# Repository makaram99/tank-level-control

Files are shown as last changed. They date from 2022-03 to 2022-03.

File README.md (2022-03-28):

<h1 align="center">Tank Level Control</h1>

      

<p align="center">
Render
</p>

<sup>
  ✅ Perform a review and leave a comment <strong><a href="https://github.com/makaram99/tank-level-control/issues/5">here</a></strong><br>
  ✅ If you want to contribute, add a new record like <a href="contributing.md">here</a><br>
  ✅ If this needs to be improved, create an issue <strong><a href="https://github.com/makaram99/tank-level-control/issues">here</a></strong>
</sup>

---

<!-- @import "[TOC]" {cmd="toc" depthFrom=1 depthTo=6 orderedList=false} -->

<!-- code_chunk_output -->
## Table of Contents
- [Table of Contents](#table-of-contents)
- [🔑 Introduction](#introduction)
- [🧮 Block Diagram](#block-diagram)
- [➗ Calculations of Distance](#calculations-of-distance)
- [🛠️ Development Tools Required](#️-development-tools-required)
- [🗻 Project Hierarchy](#project-hierarchy)
- [⚙ Working](#working)
  - [Code](#code)
  - [Simulation](#simulation)
- [📑 Generate Documentation](#generate-documentation)
- [🏭 Manufacturing](#manufacturing)
- [🎯 Results](#results)
- [🔬 What is next?](#what-is-next)
- [💁‍♂️ Contribute](#️-contribute)
- [📞 Contact me](#contact-me)
- [📖 References](#references)
- [🔓 Licenses](#licenses)
- [🔏 Credits](#credits)

<!-- /code_chunk_output -->

---

## 🔑 Introduction

Tank Level Control System is a system designed to monitor and control the level of a fluid in a tank.

If the tank gets empty and filled periodically such as in **Residential Buildings** as shown in the image below.
It will be a boring task to get a human to monitor the tank. Also, human problems such as quick response is always slower than automation system. So, the automation system is the best solution for this problem.

<p align="center">
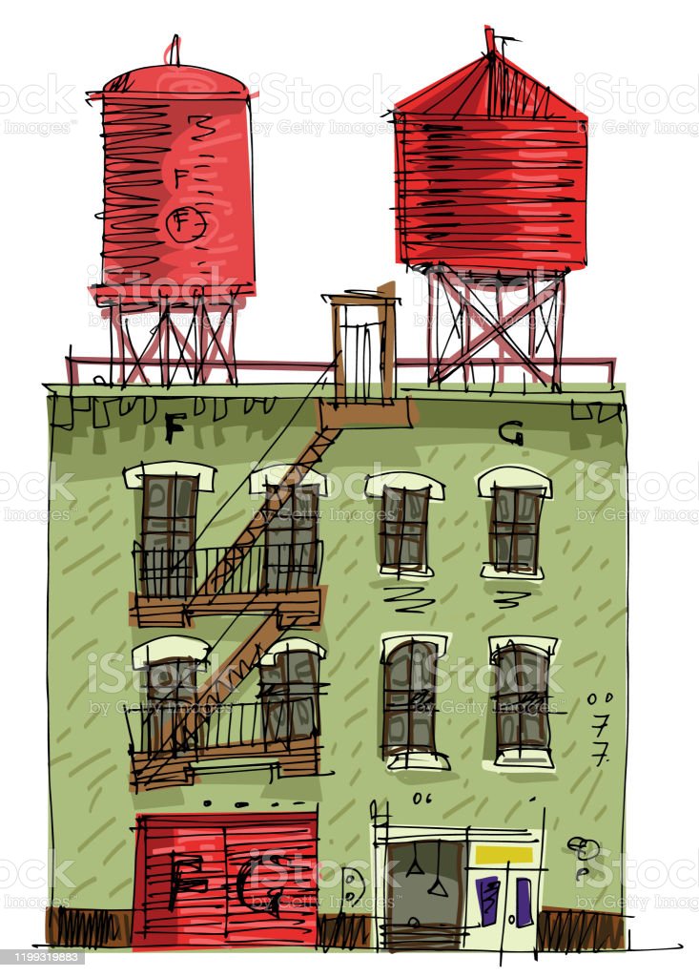
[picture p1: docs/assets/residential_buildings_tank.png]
residential_buildings_tank

</p>

It has many applications such:

1. Process tank: An important function.
2. Hot water tank: Water is removed, perhaps for washing down, and the level needs to be restored ready for the next wash cycle.

---

## 🧮 Block Diagram

<p align="center">
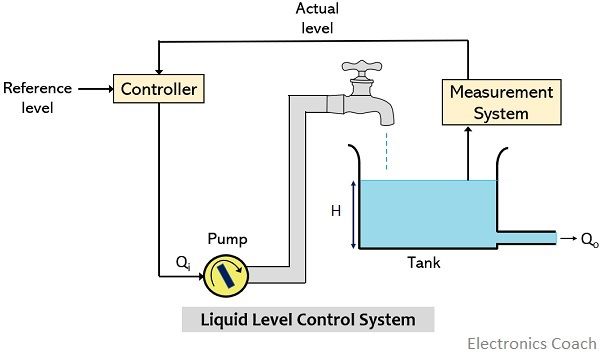
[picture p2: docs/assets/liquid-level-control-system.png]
System Construction
  
</p>

The main components of the system are:

1. **Fluid tank**: Used to hold the desired amount of fluid.
2. **Measurement system**: Senses the level of the fluid inside the tank.
3. **Controller**: Used to maintain the desired level by starting and stopping the pump depending on the information from the measurement system.
4. **Pump**: Feeds water from the source to the tank when actuated by the controller.

---

## ➗ Calculations of Distance

With the ultrasonic sensor, it sends ultrasonic waves which get beack to the sensor when hitting any surface (e.g., liquid in our case). The distance between the sensor and the surface is calculated by the following formula:

We can calculate the distance between the sensor and the surface as follows:

1. Calculate the time consumed from the instanse of sending the waves to the instance of recieving it using a timer inside the microcontroller.
2. As long as the ultrasonic waves are in fact sound waves. So, the speed of ultrasonic waves equals the speed of sound = **343 m/s**.
3. The distance between the sensor and the surface is:
   ```Distance = Speed * (Time / 2)```

4. Why the distance is divided by 2?
   The distance is divided by 2 because the waves go to the surface, then back to the sensor. So, the time calculated is the time it takes to go from the sensor to the surface and back to the sensor, hence the time must be divided by 2.

<p align="center">
  <img src="docs/assets/sensor_working.png" alt="Sensor Working"/>
</p>

---

## 🛠️ Development Tools Required

- **Toolchain**: MikroC Pro <img src="docs/assets/logo_mikro_c.png" alt="MickroC" height="40"/>

  MikroC Pro is used for code development and compiling the system.
  
  Website: [www.mikroe.com](http://www.mikroe.com/)

- **Text Editor**: <u>Visual Studio Code</u> <img src="docs/assets/logo_vscode.png" alt="VSCode" height="40"/>
  
  VS Code is used for code development. It is **free**.
  
  Download: [https://code.visualstudio.com/](https://code.visualstudio.com/)
  
- **Hardware Simulator**: <u>Proteus 8.9</u> <img src="docs/assets/logo_proteus.png" alt="Proteus" height="40"/>
  
  Proteus is used to simulate the hardware. So, no need to purchase any hardware.
  
  Download: [https://www.proteus.co.jp/](https://www.proteus.co.jp/)

- **Mechanical Design Software**: <u>SolidWorks</u> <img src="docs/assets/logo_solidworks.png" alt="SolidWorks" height="40"/>

  Website: [https://www.solidworks.com/](https://www.solidworks.com/)

- **PCB Design Software**: <u>Altium Designer</u> <img src="docs/assets/logo_altium.png" alt="Altium" height="40"/>

  Website: [https://www.altium.com/](https://www.altium.com/)

- **Documents Generator**: <u>doxygen</u> <img src="docs/assets/logo_doxygen.png" alt="doxygen" height="40"/>
  
  Doxygen is used to generate documentations of the code in html, latex, pdf, and other formats.
  
  Download: [https://www.doxygen.nl/download.html](https://www.doxygen.nl/download.html)

- **Command Line Automation Tool**: <u>make</u> <img src="docs/assets/logo_make.png" alt="make" height="40"/>
  
  Make is used to automate kernel commands.
  I've used it to automate the generation of documents from doxygen.
  
  Download:
  - Linux or MacOS: [https://www.gnu.org/software/make/](https://www.gnu.org/software/make/)
  - Windows: [http://gnuwin32.sourceforge.net/packages/make.htm](http://gnuwin32.sourceforge.net/packages/make.htm)

---

## 🗻 Project Hierarchy

The project contains some files and directories:

- **[electrical](electrical/)**: Contains everything about the electrical circuit.
  
  - [pcb](electrical/pcb): Contains PCB design of all electronics boards used in this project.
  - [simulation](electrical/simulation)**: Contains simulation files of all electronics boards used in this project.
  - [resources](electrical/resources): Contains all resources used while designing circuits.
  - [docs](electrical/docs): Contains videos of testing circuits, photos of circuits, and the pdf files describing the circuits.
  - [store_bills](electrical/store_bills): Contains store bills of components purchased for the project.
  - [bill_of_material.xlsx](electrical/bill_of_material.xlsx): Contains bill of material of components purchased for the project.
  - [version_edits.txt](electrical/version_edits.txt): Contains all bugs of the electronic circuits in the current version. So, they need to be fixed in the next version.

- **[mechanical](mechanical/)**: Contains everything about the mechanical design (Enclosure).
  - [box](mechanical/box): Contains the mechanical design of the enclosure using Solidworks.
  - [attachments](mechanical/attachments): Contains the external parts downloaded from the internet to incoroporate in the final assembly enclosure using Solidworks in the file [assembly.SLDASM](mechanical/assembly.SLDASM).
  - [arrows_keypad](mechanical/arrows_keypad), [control_circuit](mechanical/control_circuit), and [power_circuit](mechanical/power_circuit): Step files of the electronics circuits [here](electrical/simulation), to incoroporate in the final assembly enclosure using Solidworks in the file [assembly.SLDASM](mechanical/assembly.SLDASM).
  - [assembly.SLDASM](mechanical/assembly.SLDASM): Contains the final assembly of the projects containing enclosure, electronic circuits, and attachments.
  - [assembly_drawing.SLDDRW](mechanical/assembly_drawing.SLDDRW): Contains the drawing file generated by Solidworks for the assembly.
  - [final_assembly.PDF](mechanical/docs/final_assembly.PDF): Contains dimension, and different views of the assembly. It is generated from the file [final_assembly.PDF](mechanical/docs/final_assembly.PDF).

- **[software](software/)**: Contains everything about the code.
  - [code](software/code): Contains the code of the project.
  - [resources](electrical/resources): Contains all resources used while designing circuits.
  - [problems.txt](software/problems.txt): Contains documentation of some problems occuredd while testing the system physically.
  - [version_edits.txt](software/version_edits.txt): Contains all bugs of the code in the current version. So, they need to be fixed in the next version.

- **[docs](docs/)**: Contains the documentation generated using doxygen and make, and other documents designed by me.
- **[README.md](README.md)**: Contains the introduction of the project (What you are reading now).
- **[LICENSE](LICENSE)**: Contains the license of the project.
- **[Doxyfile](Doxyfile)**: Contains the configuration of doxygen (Documentation generator).
- **[doxygen.mk](doxygen.mk)**: Contains the configuration and rules to be run using make to generate documents.
- **[Makefile](Makefile)**: Contains the configuration and rules to be run using make to automate buil process of the software (compile, flash, clean, ...) documents.
- **[steps_of_project.pdf](steps_of_project.pdf)**: Contains the block diagram of steps of the project.

---

## ⚙ Working

### Code

To develop the project (code), you need to:

- YOU MUST HAVE **(MikroC Pro) or (Visual Studio Code with XC8 PIC Compiler)** installed on your computer.
- Open the [code](software/code) directory.
- If you have:
  - MikroC Pro: Click twice on **[tankLevel.mcppi](tankLevel.mcppi)** file. It will open with Mikro C Pro.
  - Visual Studio Code with XC8 compiler: Open the project with VS Code.
- Enjoy the development.
- To build the project, if you have:
  - MikroC Pro: Click on **Build button** on quick access bar of MikroC Pro, or press **Ctrl + F9** on the keyboard.
  - Visual Studio Code with XC8 compiler:
    - Open the terminal inside VS Code by pressing on **Ctrl + `** on the keyboard.
    - Type the command ```make all```. It will compile the project.
    - The hex file will be generated in the [code](software/code) directory with the name **app.hex**.
    - To flash the hex file to the PIC, type the command ```make flash```.
    - To remove the output files (hex and intermediate files), type the command ```make clean```.

**NOTE**: I've documented the code as much as I can. So, I hope you will understand the code.

### Simulation

To simulate the project, you need to:

- YOU MUST HAVE **Proteus** installed on your computer.
- Proteus has **compatibility issues** with its version, and the project may not be opened if you have a different version of proteus. So, you need to install **Proteus 8.9** to be able to simulate the project.
- From the [simulation](electrical/simulation) directory, open the folder of any of the boards.
- Click twice on the file ends with **[.pdsprj](simulation/simulation.pdsprj)**.
- It will open with Proteus as shown here:
  - Control Circuit
   <img src="electrical/docs/test_simulation/simulation_control_circuit.gif" alt="simulation_control_circuit"/>
  - Power Circuit
   <img src="electrical/docs/test_simulation/simulation_power_circuit.gif" alt="simulation_power_circuit"/>

- As shown in the Control Circuit, it is divided into blocks such as Controller, PUMP, and Sensor blocks.

- To run simulation, click on **F12** from the keyboard.
- Increase/Decrease the distance measured by the ultrasoni sensor by pressing Up/Down arrow on the Sensor block. The distance measured by the sensor will be displayed on the LCD screen as a percentage representing the level percentage of the tank. The percentage depends on a predetermined value equals to the height of the tank (in our case, the tank is 24cm height).
- When the percentage is lower than 15%, the pump will be turned on.
- When the percentage is higher than 80%, the pump will be turned off.
- When the percentage is between 15% and 80%, the pump will be latched to the last state. If the pump was on, it will be remains on. If the pump is off, it will remains off.
- To stop the simulation: Press twice on **ESC** key from the keyboard.

**NOTE**: The keypad is not used in the current version of the project. It is put for future use.

---

## 📑 Generate Documentation

To generate documentation:

1. YOU MUST HAVE **DOXYGEN** AND **MAKE** INSTALLED ON YOUR COMPUTER.
2. From the home directory of the project (**tank_level_control**), open the command prompt in your OS (**cmd** for Windows, **bash** for linux, ...)
3. Run the following command:
   ```make -f doxygen.mk all```
4. The documentation will be generated in the **[docs](docs)** directory.

---

## 🏭 Manufacturing

**Here is a comparison between CAD design on Solidworks versus the final physical shape:
**

1. Product:

  <img src="mechanical/docs/box_cad_vs_real_view2.png" alt="Enclosure" width="500"/>
2. Control Circuit:

  <img src="mechanical/docs/control_circuit_cad_vs_reality.png" alt="Control" width="500"/>
3. Power Circuit:

  <img src="mechanical/docs/power_circuit_cad_vs_real.png" alt="Power" width="500"/>
4. Keypad:

  <img src="mechanical/docs/keypdad_cad_vs_reality.png" alt="Keypad" width="500"/>

---

## 🎯 Results

After running the project either on the simulation (Proteus) or running the physical hardware. The result was as expected. So, you also can use the project and it will work as expected.

You can check the working of the project by opening the [test_project.m4v](electrical/docs/test_videos/test_project.m4v) file.

If you want to check operation of each circuit, open:

- [test_power_circuit.m4v](electrical/docs/test_videos/test_power_circuit.m4v) to see the working of power circuit.
- [test_kit.m4v](electrical/docs/test_videos/test_kit.m4v) to see the working of control circuit.
- [test_short_circuit.m4v](electrical/docs/test_videos/test_short_circuit.m4v) to see the working of short circuit protection.

---

## 🔬 What is next?

I will always try to improve this project.
***Next Version***: Features of the next version can be found in the file [version_edits.txt](software/version_edits.txt) in [software](software/) directory.

---

## 💁‍♂️ Contribute

If you want to contribute to the project, add a new record like <a href="contributing.md">here</a><br>

## 📞 Contact me

<p><a href="https://www.linkedin.com/in/makaram99" target="_blank"><img alt="LinkedIn" src="https://img.shields.io/badge/linkedin-%230077B5.svg?&style=for-the-badge&logo=linkedin&logoColor=white" /></a> <a href="mailto:ma.karam272@gmail.com" target="_blank"><img alt="Gmail" src="https://upload.wikimedia.org/wikipedia/commons/thumb/7/7e/Gmail_icon_%282020%29.svg/640px-Gmail_icon_%282020%29.svg.png" height="30" /></a> </p>

## 📖 References

- Resources used can be found in resources directories inside [software](software/), [mechanical](mechanical/), and [electrical](electrical/) directories.

## 🔓 Licenses

<br />All DOCUMENTS inside this work is licensed under a <a rel="license" href="http://creativecommons.org/licenses/by-sa/4.0/">Creative Commons Attribution-ShareAlike 4.0 International License</a>.

All SOURCE codes & BINARIES are licensed under Mit License.

<p align="center">
  <img alt="Creative Commons Licence" style="border-width:0" src="https://i.creativecommons.org/l/by-sa/4.0/88x31.png" />
</p>

<p align="center">
  <img src="https://img.shields.io/badge/license-Mit%20-blue" alt="license"/>
</p>

## 🔏 Credits

All credits and external sources are listed inside the page and inside this repo, references themselves.

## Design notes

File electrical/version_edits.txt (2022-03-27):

Version 2:
	Control Circuit:
		1. Edit GPIOs pin headeres' Letters.
		2. Remove residual diode on relay interface.
		3. Use dip-switches instead of jumpers for peripherals power closer to main power leads and use indication LEDs.
	
	Power Circuit:
		1. Edit footprint of LM317 for easy soldering.
		2. Reverse voltage signs and o/p connector.
		3. Increase Border area to avoid screw' holes distortion.
		4. Add pin header for far access to Latch button.
		5. Add pin header for dfar access for fuse.
		6. Buy components first to modify overlay.

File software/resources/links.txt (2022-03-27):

Ultrasonic HC-SR04 Working Principles				: https://www.youtube.com/watch?v=08dcoXZEtqs&feature=youtu.be
Ultrasonic HC-SR04 Apps								: https://www.youtube.com/watch?v=pwWk20du8qA
Tank Level indicator with Arduino					: https://www.youtube.com/watch?v=08dcoXZEtqs&feature=youtu.be
Interfacing HC-SR04 Ultrasonic Sensor with PIC MCU	: https://electrosome.com/hc-sr04-ultrasonic-sensor-pic/
Timer1 Working										: https://www.youtube.com/watch?v=up78Mm74ag0
													: https://www.youtube.com/watch?v=gUT-0IAoh2I&t=7s

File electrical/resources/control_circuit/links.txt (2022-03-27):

Items prefixed by // is optional to see.

Protection:
	//AC overvoltage					: https://circuitdigest.com/electronic-circuits/230v-ac-mains-over-voltage-protection-circuit
	//Overcurrent with op-amp			: https://circuitdigest.com/electronic-circuits/overcurrent-protection-circuit-using-op-amp#comments
	//Short circuit with restart button	: https://circuitdigest.com/electronic-circuits/short-circuit-protection-circuit-diagram#
	Reverse polarity					: Used: https://www.youtube.com/watch?v=IrB-FPcv1Dc
										: https://circuitdigest.com/electronic-circuits/reverse-polarity-protection-circuit-diagram

Circuits:
	PSU (1-25)V, 10A with cooling fan	: https://www.youtube.com/watch?v=q39YfcpMyRY

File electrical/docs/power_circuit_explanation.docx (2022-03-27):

Variable PSU with LM317T

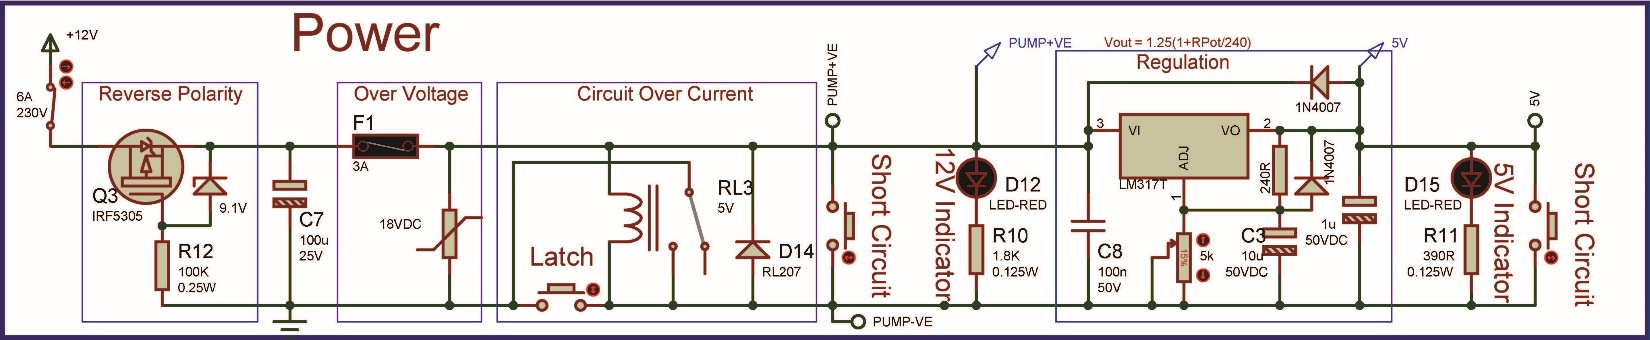
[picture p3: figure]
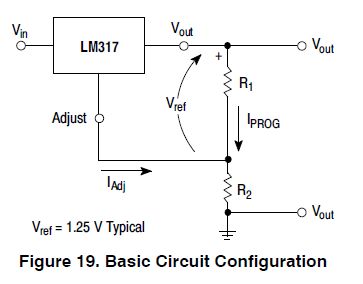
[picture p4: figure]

LM317:

Basics of LM317:

It’s:

1. Short circuit proof (shutdown).
2. Over temperature shutdown.
3. Floating Operation for High Voltages.

LM317 generate a difference of 1.25V between V_(out) and Adjustable pins ( V_(ref) =1.25V) .

∵ V_(out) =V_(R_1) +V_(R_2) =I_(PROG) (R_1 +R_2 )+I_(Adj) R_2

∵ I_(PROG) =(V_(ref))/(R_1) substitute I_(PROG)

∴ V_(out) =(V_(ref))/(R_1)(R_1 +R_2 )+I_(Adj) R_2 =V_(ref) (1+(R_2)/(R_1))+I_(Adj) R_2

Because V_(ref) is constant and I_(PROG) must be constant. So, R_1 must be constant, and then, we can control the O/P with R_2 value.

But the term I_(Adj) R_2 is not desired cuz we can’t control it. So, LM317 control it to be less than 100uA which is negligible. So:

V_(out) =V_(ref) (1+(R_2)/(R_1)) 120≤R_1 ≤1000

Often, R_1 =240 which give the best results.

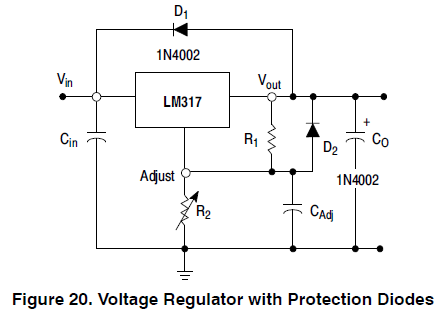
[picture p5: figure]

Tips for LM317 circuit design:

R_2 selection:

R_2 should make V_(out(max)) ≤37V (max of IC )

∵ [V_(out(max)) =V_(ref) (1+(R_2)/(R_1))]≤37V

∴ R_2 ≤(37/(V_(ref))-1)*R_1

Often, R_1 =240Ω give the best results.

∴ R_2 ≤(37/1.25-1)*240=6864Ω

- We need V_(out(min)) =3V . So, we will put a fixed resistor with the trimmer in case of making it’s resistor = 0.

R_(fixed) =(3/1.25-1)*240=336⋍330Ω

- Cuz we don’t need to reach 37V in practical apps, we will choose the value of the trimmer to be R_2 = 5KΩ, making

V_(out(max)) =1.25(1+(5000+330)/240)⋍29V

Capacitors:

1. C_(in) of (0.1uF disc or 1.0uF tantalum) is recommended to reduce the sensitivity to input line impedance.
2. C_(Adj) is recommended to bypass the adjustment terminal to ground to improve ripple rejection. It prevents ripple being amplified as the output voltage is increased. A 10uF disc capacitor improves ripple rejection about 15 dB at 120 Hz in a 10 V application.
3. LM317 is stable with no output capacitance. But certain values of external capacitance can cause excessive ringing. C_O of (1.0uF tantalum or 25uF aluminum electrolytic) swamps this effect and insures stability.

Protection Diodes:

Protection diodes must be used when capacitors are used to prevent discharging through low current points into the regulator.

1. D_1 prevents C_O discharging thru the IC during an I/P short circuit.
2. D_2 prevents C_(Adj) discharging thru the IC during an O/P short circuit.
3. D_1 with D_2 prevents C_(Adj) discharging thru the IC during an I/P short circuit.

When V_(in) ≥40

LM317 can have its output shorted without damage. But -0.3V≤(V_(in) - V_(out) )≤40V . So, applying 45V to the input, and getting 30V from the output. A 15V appears over the IC which is fine, but if the output gets shorted somehow (i.e. the initial charging of large capacitors C_O ), a full 45V appears above the IC and this is enough to damage it(>40V).

Solution: (https://electronics.stackexchange.com/questions/148340/how-to-protect-lm317-from-output-short/148342)

Replace D1 with a 30V zener rated for several amps(P6KE30A), and a fuse (before Vin) to blow before the zener.

- Normal operation: the zener should not normally conduct.
- Power-off operation: the zener is forward biassed providing the same protection D1 does.
- Power-on operation: with 45V in, the zener will supply current to the load if the LM317 is supplying less than 15V. After that, the LM317 takes over.
- Short circuit operation: the IC goes into current limit and the output voltage drops. The zener conducts before I/O voltage exceeds 40V. The fuse blows.

Tips for LM317 PCB design:

1. R_1 should be connected close to the regulator pins to minimize line drops which appears in series with V_(ref) , thereby degrading regulation.
2. The ground end of R_2 should be connected close to the load ground to provide remote ground sensing and improve load regulation.
3. C_(in) and C_O should be connected close to the IC pins to avoid stray inductance.

Resources:

LM317: → Basic : (39) LM317: How It Works and Why You Need It (Ep. 2) - YouTube (https://www.youtube.com/watch?v=Kw1IxR5K_gk)

→ Increase current: (39) LM317: How To Increase Amperage (Ep. 3) - YouTube (https://www.youtube.com/watch?v=2W51oVesKP8)

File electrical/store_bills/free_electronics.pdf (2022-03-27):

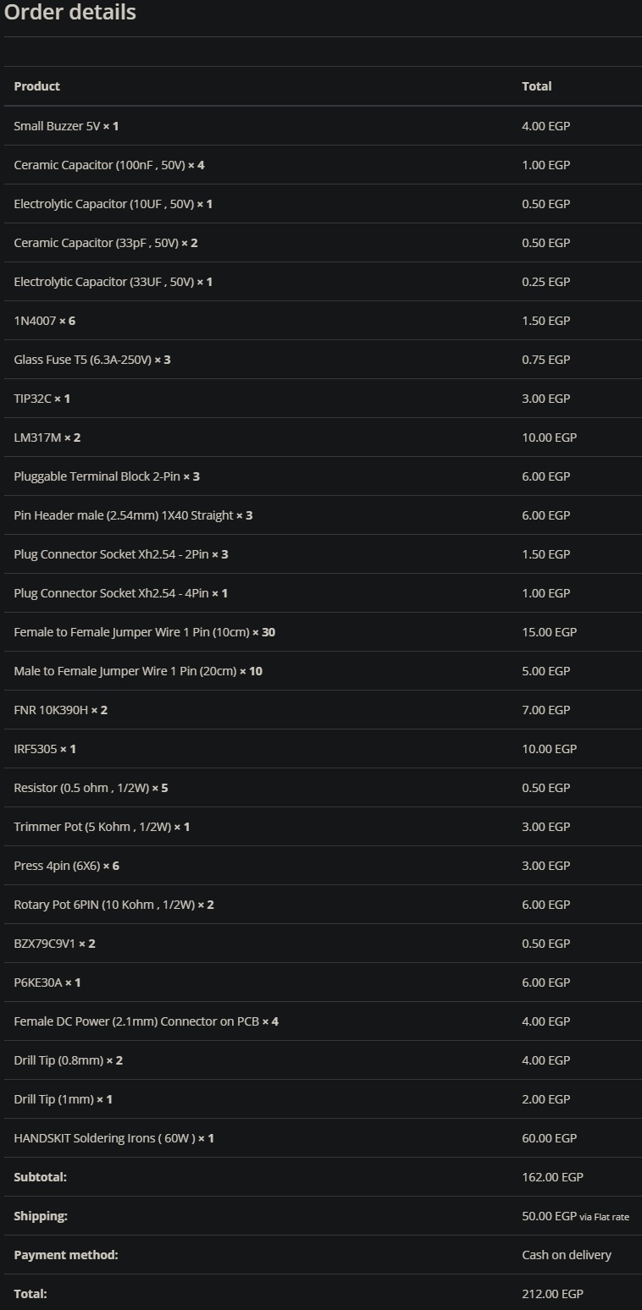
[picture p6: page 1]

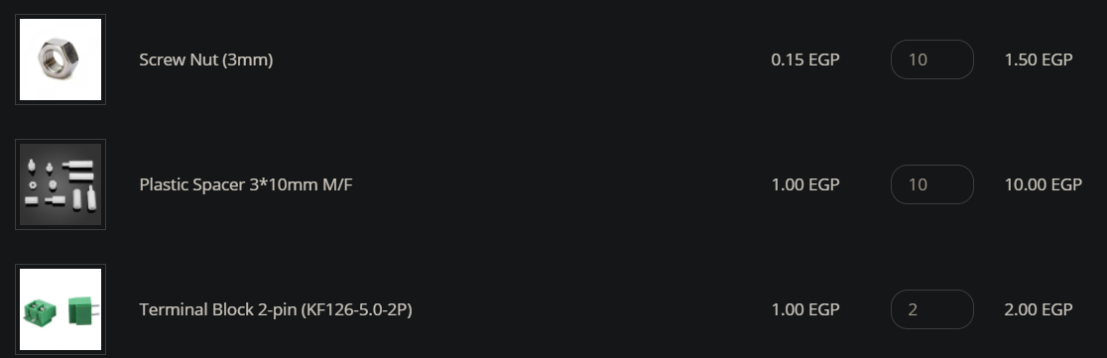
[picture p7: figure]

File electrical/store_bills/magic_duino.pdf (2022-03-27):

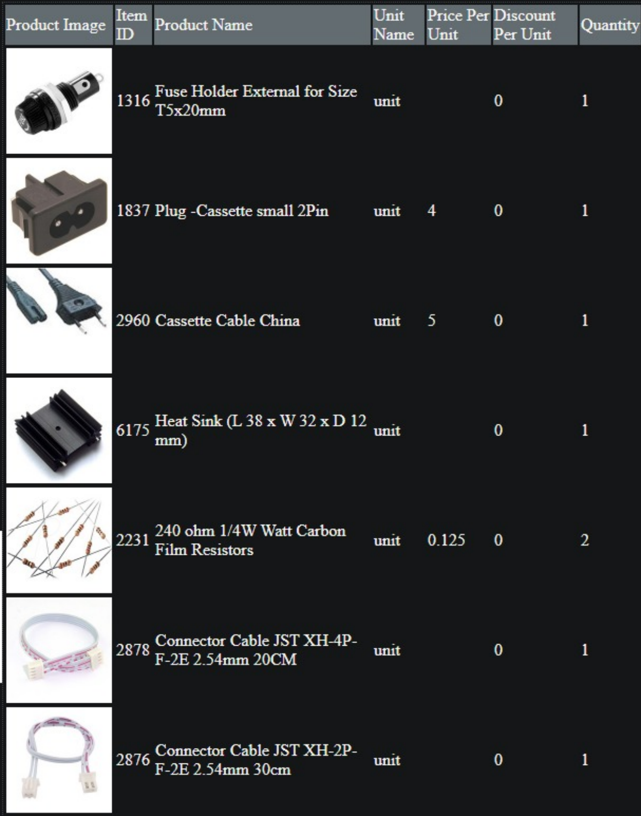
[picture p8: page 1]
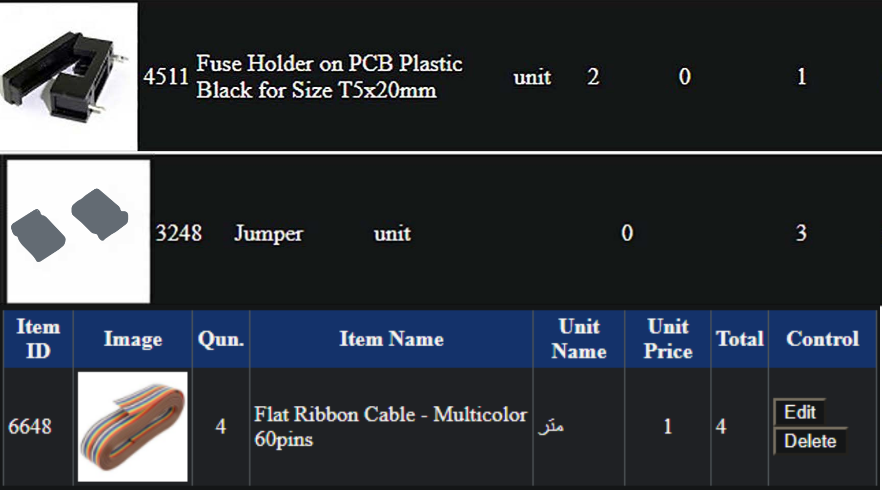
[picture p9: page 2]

••

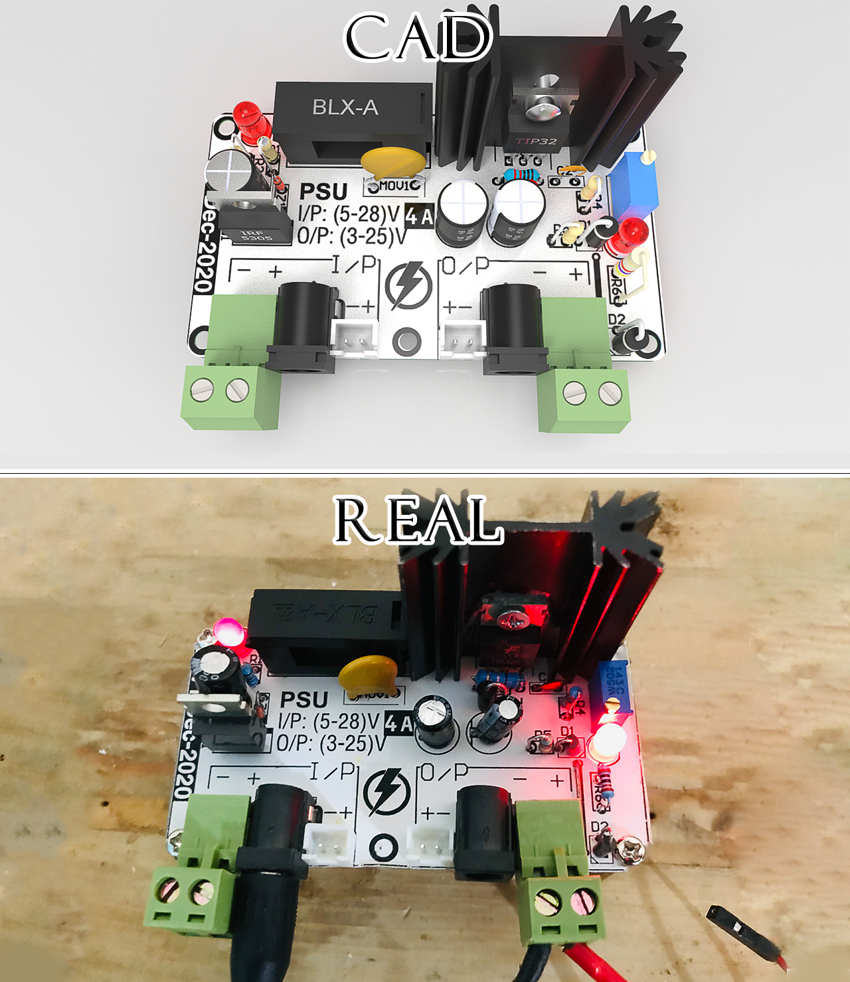
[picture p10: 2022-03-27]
mechanical/docs/power_circuit_cad_vs_real.png

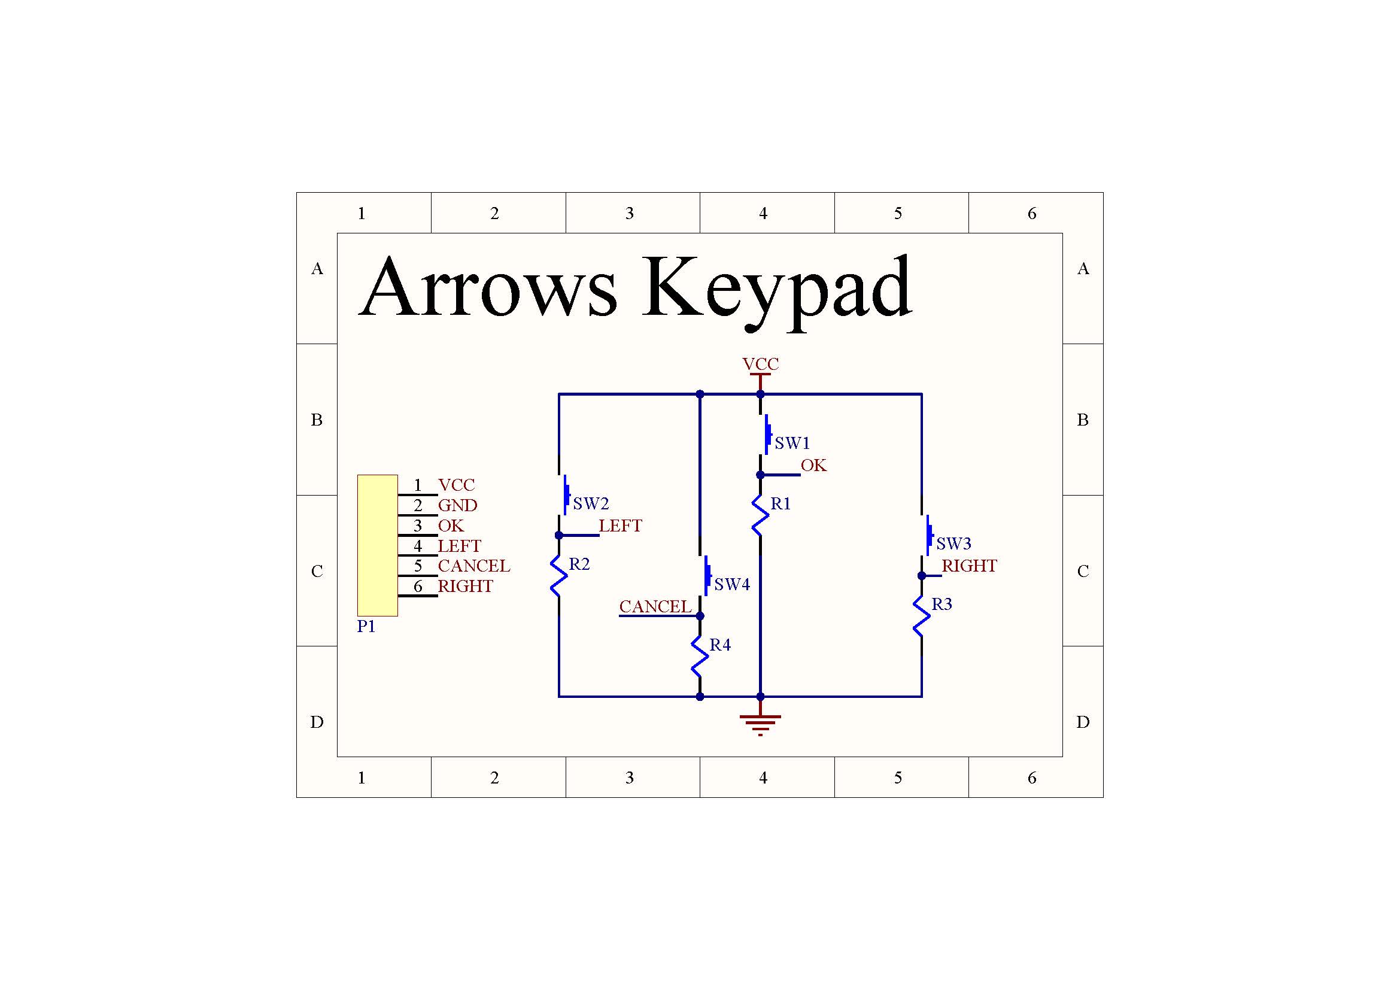
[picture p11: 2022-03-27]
electrical/docs/pdf/arrows_keypad_schematic.jpg

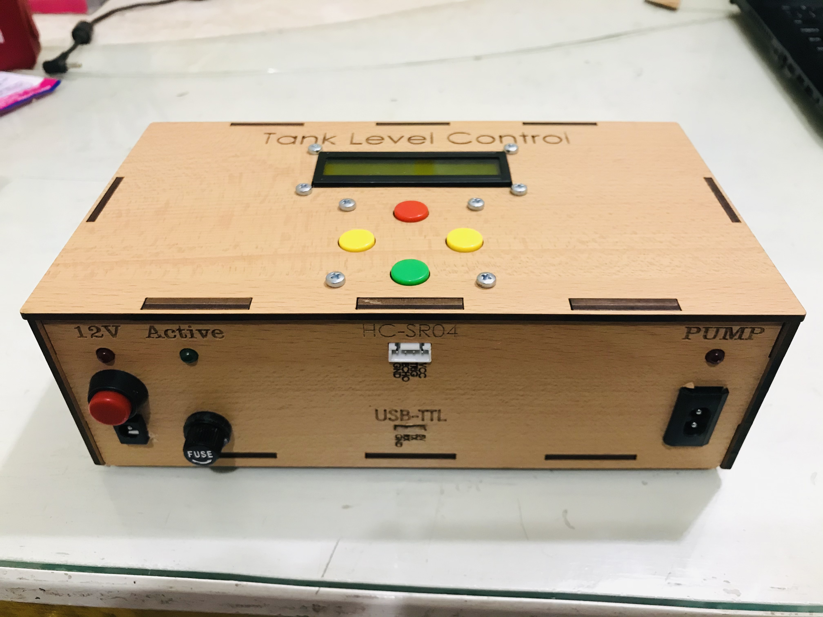
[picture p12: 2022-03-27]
mechanical/docs/box_real_view6.png

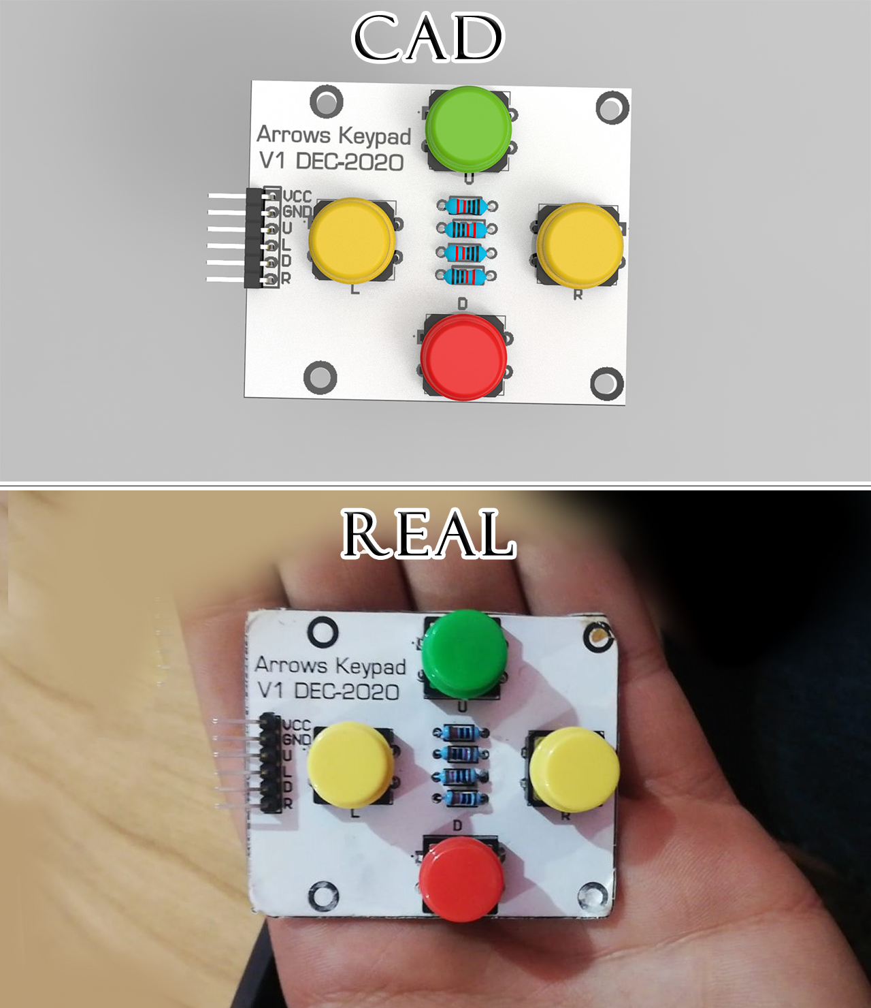
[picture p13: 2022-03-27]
mechanical/docs/keypdad_cad_vs_reality.png

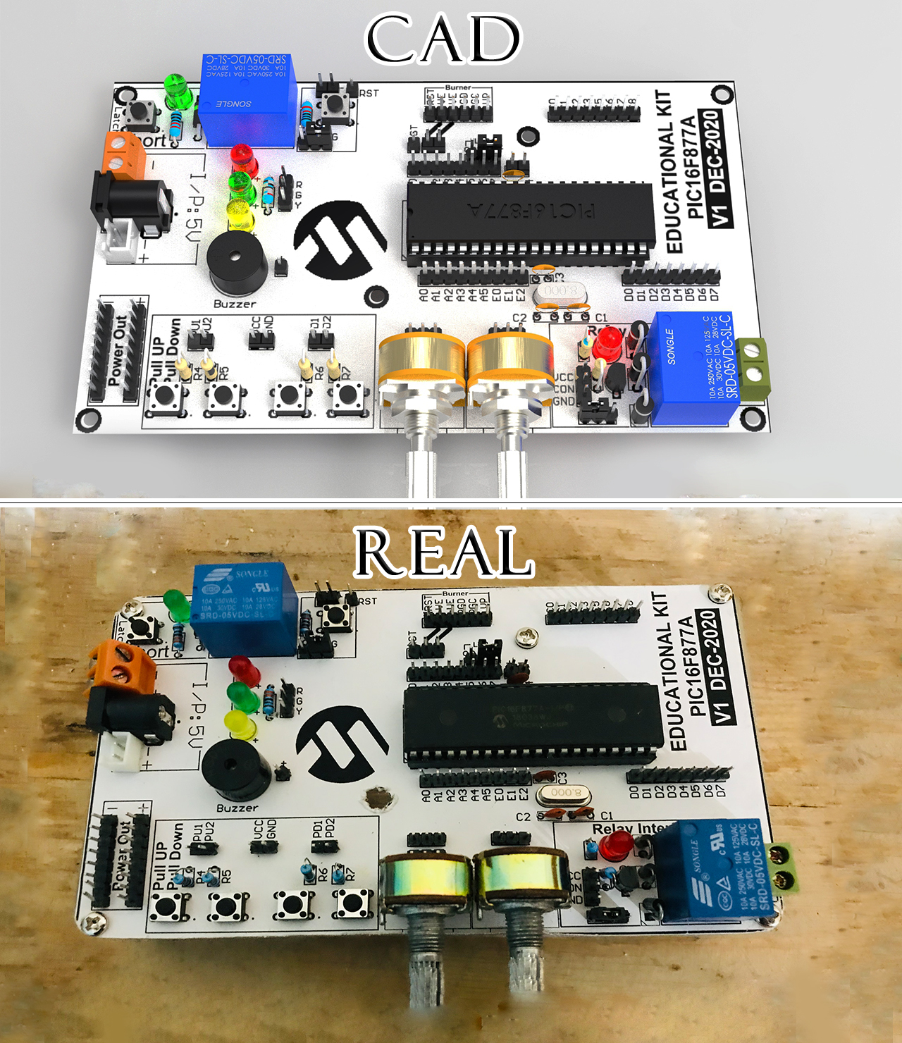
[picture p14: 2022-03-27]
mechanical/docs/control_circuit_cad_vs_reality.png

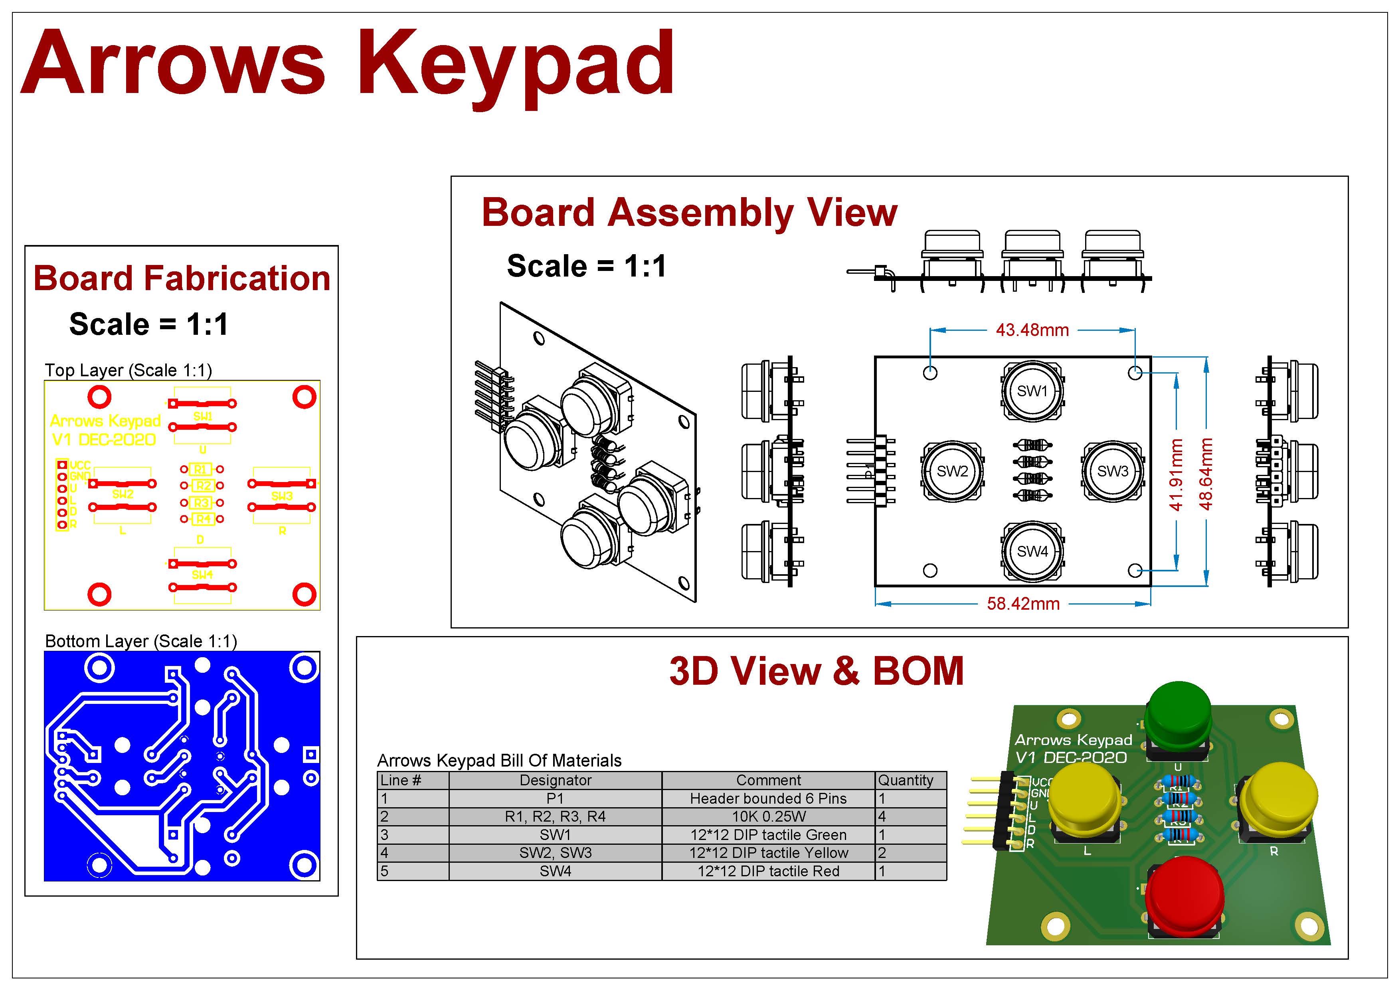
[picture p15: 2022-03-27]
electrical/docs/pdf/arrows_keypad_schematic_details.jpg

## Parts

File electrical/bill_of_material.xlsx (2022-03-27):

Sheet: Sheet1
Component | With Us or Buy | # | Websites |  |  | Best Price
 |  |  | Free (https://free-electronic.com/) | Magic (http://magicduino.com/Default.aspx) | RAM (https://ram-e-shop.com/)
Buzzer 5V | Buy | 1 | 4 (https://free-electronic.com/product/small-buzzer-5v/) | 5 (http://magicduino.com/ProDetails.aspx?ID=1796) | 5 (https://ram-e-shop.com/product/buzzar6v/) | Free
Capacitor 100nF 50V | Buy | 4 | 0.25 (https://free-electronic.com/product/ceramic-capacitor-100nf-50v/) | 0.25 (http://magicduino.com/ProDetails.aspx?ID=1992) | 0.25 (https://ram-e-shop.com/product/c-pf-104/) | Free
Capacitor 100uF 50V | Buy | 1 | 0.75 (https://free-electronic.com/product/electrolytic-capacitor-100uf-50v/) | 0.5 (http://magicduino.com/ProDetails.aspx?ID=2079) | 0.6 (https://ram-e-shop.com/product/c-100u50v/) | Magic
Capacitor 10uF 50V disc | Buy | 1 | 0.5 (https://free-electronic.com/product/electrolytic-capacitor-10uf-50v/) | 0.5 (http://magicduino.com/ProDetails.aspx?ID=2049) | 0.5 (https://ram-e-shop.com/product/c-10u50v/) | Free
Capacitor 33pF 50V | Buy | 2 | 0.25 (https://free-electronic.com/product/ceramic-capacitor-33pf-50v/) | 0.25 (http://magicduino.com/ProDetails.aspx?ID=1925) | 0.25 (https://ram-e-shop.com/product/c-pf-33/) | Free
Capacitor 33uF 50V Electrolyte | Buy | 1 | 0.25 (https://free-electronic.com/product/electrolytic-capacitor-33uf-50v/) | 0.5 (http://magicduino.com/ProDetails.aspx?ID=2030) | 0.5 (https://ram-e-shop.com/product/c-33u50v/) | Free
Diode 1N4007 | Buy | 6 | 0.25 (https://free-electronic.com/product/1n4007/) | 0.25 (http://magicduino.com/ProDetails.aspx?ID=1611) | 0.35 (https://ram-e-shop.com/product/1n4007/) | Free
Fuse 6A T5*20 (https://free-electronic.com/product/glass-fuse-t5-6-3a-250v/) | Buy | 1 | 0.25 (https://free-electronic.com/product/glass-fuse-t5-6-3a-250v/) | 0.5 (http://magicduino.com/ProDetails.aspx?ID=1774) | 0.5 (https://ram-e-shop.com/product/fuse6a/) | Free (https://ram-e-shop.com/product/fuse6a/)
Fuse Holder T5*20 Floating | Buy | 1 | NA | Call (http://magicduino.com/ProDetails.aspx?ID=1316) | NA | Magic
Fuse Holder T5*20 PCB | Buy | 1 | NA | 2 (http://magicduino.com/ProDetails.aspx?ID=4511) | NA | Magic
Heatsink TO-220 38*32*12 | Buy | 1 | 7 (https://free-electronic.com/product/heatsink-34x12x25mm/) | Call (http://magicduino.com/ProDetails.aspx?ID=6175) | NA | Magic
PNP TIP32C 3A | Buy | 1 | 3 (https://free-electronic.com/product/tip32c/) | 4 (http://magicduino.com/ProDetails.aspx?ID=728) | NA | Free
Regulator LM317M 1.5A SMT | Buy | 1 | 5 (https://free-electronic.com/product/lm317m/) | NA | NA | Free
PIC16F877A | Ma. Karam | 1 | 50 (https://free-electronic.com/product/pic16f877a-ip/) | Call (http://magicduino.com/ProDetails.aspx?ID=1079) | 50 (https://ram-e-shop.com/product/pic16f877a-ip/) | Magic
Socket DIP 40Pins 2.54mm | Ma. Karam | 1 | 1 (https://free-electronic.com/product/ic-socket-base-40-pin-dip/) | 1.5 (http://magicduino.com/ProDetails.aspx?ID=1135) | 1.5 (https://ram-e-shop.com/product/n20-20/) | Free
Pluggable Terminal BLock 2pins | Buy | 3 | 2 (https://free-electronic.com/product/pluggable-terminal-block-2-pin/) | 2 (http://magicduino.com/ProDetails.aspx?ID=1333) | 2 (https://ram-e-shop.com/product/rc2-2pin-connected/) | Free
DC Barrel Power Jack 2.1mm | Buy | 4 | 1 (https://free-electronic.com/product/female-dc-power-2-1mm-connector-on-pcb/) | 2 (http://magicduino.com/ProDetails.aspx?ID=7053) | 1.5 (https://ram-e-shop.com/product/dc-soket/) | Free
Pin header male 40pins | Buy | 3 | 2 (https://free-electronic.com/product/pin-header-male-2-54mm-140-straight/) | 2 (http://magicduino.com/ProDetails.aspx?ID=1701) | 3 (https://ram-e-shop.com/product/2-54mm-0-100-pin-header-male-1x40-straight-yellow/) | Free
Cassette cable male | Buy | 1 | 10 (https://free-electronic.com/product/ac-power-cord/) | 5 (http://magicduino.com/ProDetails.aspx?ID=2960) | NA | Magic
Plug Cassette 2pins 220VAC | Buy | 1 | NA | 4 (http://magicduino.com/ProDetails.aspx?ID=1837) | NA | Magic
Socket Xh2.54 2pins | Buy | 3 | 0.5 (https://free-electronic.com/product/plug-connector-socket-xh2-54/) | 0.5 (http://magicduino.com/ProDetails.aspx?ID=1804) | NA | Free
cable Xh2.54 male-male 2pins | Buy | 1 | 1 (https://free-electronic.com/product/plug-connector-wire-xh2-54/) | 1 (http://magicduino.com/ProDetails.aspx?ID=2876) | NA | Magic
Socket Xh2.54 4pins | Buy | 1 | 1 (https://free-electronic.com/product/plug-connector-socket-xh2-54/) | Call (http://magicduino.com/ProDetails.aspx?ID=1806) | NA | Free
Cable Xh2.54 male-male 4pins | Buy | 1 | NA | Call (http://magicduino.com/ProDetails.aspx?ID=2878) | NA | Magic
Jumper Female to Female 10cm | Buy | 30 | 0.5 (https://free-electronic.com/product/female-to-female-jumper-wire-40-pin-10cm/) | NA | NA | Free
Jumper Female to Female 20cm | Buy | 10 | 0.5 (https://free-electronic.com/product/male-to-female-jumper-wire-40-pin-20cm/) | 0.75 (http://magicduino.com/ProDetails.aspx?ID=6054) | 0.5 (https://ram-e-shop.com/product/ph62-ff-20cm/) | Free
Terminal BLock 2pins | Mo. 3la' | 1 | 1 (https://free-electronic.com/product/terminal-block-2-pin-kf126-5-0-2p/) | 1.25 (http://magicduino.com/ProDetails.aspx?ID=1322) | 1.5 (https://ram-e-shop.com/product/2-pin-pcb-r5-long/) | Free
LED Red 5mm (2.7 ~ 3.6)V | Mo. 3la' | 4 | 0.25 (https://free-electronic.com/product/led-red-color-5mm/) | 0.25 (http://magicduino.com/ProDetails.aspx?ID=1693) | 0.25 (https://ram-e-shop.com/product/led-rr/) | Free
LED Green 5mm (2.7~3.6)V | Mo. 3la' | 2 | 0.25 (https://free-electronic.com/product/led-green-color-5mm/) | 0.25 (http://magicduino.com/ProDetails.aspx?ID=1694) | 0.25 (https://ram-e-shop.com/product/led-gg/) | Free
LED Yellow 5mm (2.7~3.6)V | Mo. 3la' | 1 | 0.25 (https://free-electronic.com/product/led-yellow-color-5mm/) | 0.25 (http://magicduino.com/ProDetails.aspx?ID=1695) | 0.25 (https://ram-e-shop.com/product/led-gg/) | Free
MOV 30VDC 10mm | Buy | 1 | 3.5 (https://free-electronic.com/product/fnr-10k390h/) | NA | NA | Free
P-Channel IRF5305 | Buy | 1 | 10 (https://free-electronic.com/product/irf5305/) | NA | NA | Free
Transistor 2N2222 (0.8A - 30V) | 3bdo | 1 | 0.5 (https://free-electronic.com/product/2n2222a/) | 0.5 (http://magicduino.com/ProDetails.aspx?ID=28) | 0.5 (https://ram-e-shop.com/product/2n2222/) | Free
Resistor 100K 1/4W | Sally | 1 | NA | 0.125 (http://magicduino.com/ProDetails.aspx?ID=2328) | NA | Magic
Resistor 330 1/4W | Sally | 4 | 0.05 (https://free-electronic.com/product/resistor-330-ohm-1-4w/) | 0.125 (http://magicduino.com/ProDetails.aspx?ID=2236) | 0.1 (https://ram-e-shop.com/product/fixed-resistances-49/) | Free
Resistor 1.5k 1W | Buy | 2 | 0.25 (https://free-electronic.com/product/resistor-1-5-kohm-1w/) | NA | NA | Free
Resistor 0.5R 0.5W | Buy | 1 | 0.1 (https://free-electronic.com/product/resistor-0-5-ohm-1-2w/) | 0.15 (http://magicduino.com/ProDetails.aspx?ID=2399) | NA | Free
Resistor 240R 1/4W | Buy | 1 | NA | 0.125 (http://magicduino.com/ProDetails.aspx?ID=2231) | 0.1 (https://ram-e-shop.com/product/fixed-resistances-45/) | Magic
Resistor 10K 1/4W | Sally | 5 | NA | 0.125 (http://magicduino.com/ProDetails.aspx?ID=2294) | NA | Magic
Resistor 560R 1/4W | Mo. 3la' | 1 | 0.05 (https://free-electronic.com/product/resistor-560-ohm-1-4w/) | 0.125 (http://magicduino.com/ProDetails.aspx?ID=2247) | 0.1 (https://ram-e-shop.com/product/fixed-resistances-55/) | Free
Trimmer 5KR | Buy | 1 | 3 (https://free-electronic.com/product/trimmer-pot-5-kohm-1-2w/) | 2.75 (http://magicduino.com/ProDetails.aspx?ID=4802) | 1.25 (https://ram-e-shop.com/product/pot-5k-small/) | Free
Rocker Switch 6A | 3bdo | 1 | 1 (https://free-electronic.com/product/boat-rocker-switch-on-off-6a250vac-kcd1/) | Call (http://magicduino.com/ProDetails.aspx?ID=1205) | 2.5 (https://ram-e-shop.com/product/dc-soket/) | Free
Tactile Switch 6*6*15 | Buy | 1 | NA | Call (http://magicduino.com/ProDetails.aspx?ID=5951) | 2 (https://ram-e-shop.com/product/press-4pin-push-button-6x6x15-mm-tack-switch-standard-type/) | Magic
Tactile Switch 6*6*5.5 | Buy | 6 | 0.5 (https://free-electronic.com/product/press-4pin-6x6/) | 0.5 (http://magicduino.com/ProDetails.aspx?ID=6515) | NA | Free
Potentiometer dual 10KR 1/2W | Buy | 2 | 3 (https://free-electronic.com/product/rotary-pot-6pin-10-kohm-1-2w/) | NA | NA | Free
Zener 9.1V (BZX79C9V1) | Buy | 1 | 0.25 (https://free-electronic.com/product/bzx79c9v1/) | 0.5 (http://magicduino.com/ProDetails.aspx?ID=1522) | NA | Free
Zener 30V (P6KE30A) | Buy | 1 | 6 (https://free-electronic.com/product/p6ke30a/) | NA | NA | Free
Crystal 2-PIN (8 MHz) | Mo. 3la' | 1 | 3 (https://free-electronic.com/product/crystal-2-pin-8-mhz/) | 3 (http://magicduino.com/ProDetails.aspx?ID=1171) | 3 (https://ram-e-shop.com/product/o-8mhz/) | Free
Adapter 12v 2A | Sally | 1 | NA | NA | 60 (https://ram-e-shop.com/product/adaptor-fixed-12v-2a/) | RAM
Relay 5V | Mo. 3la' | 2 | 5 (https://free-electronic.com/product/relay-srd-05vdc-sl-c/) | Call | 7 (https://ram-e-shop.com/product/re15/) | Free
Ultrasonic HC-SR04 | Ma. Karam | 1 | 35 (https://free-electronic.com/product/ultrasonic-sensor-hc-sr04/) | 45 (http://magicduino.com/ProDetails.aspx?ID=5613) | 38 (https://ram-e-shop.com/product/kit-ultrasonic-txrx/) | Free
LCD character 16*2 Blue | Ma. Karam | 1 | 40 (https://free-electronic.com/product/lcd1602-blue-backlight-with-soldering-pin-header/) | 45 (http://magicduino.com/ProDetails.aspx?ID=1146) | 45 (https://ram-e-shop.com/product/lcd-2x16-blue/) | Free
PCB FR4 20*15 single layer | Mo. 3la' | 1

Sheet: Done
#VALUE!

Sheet: Still
#VALUE!

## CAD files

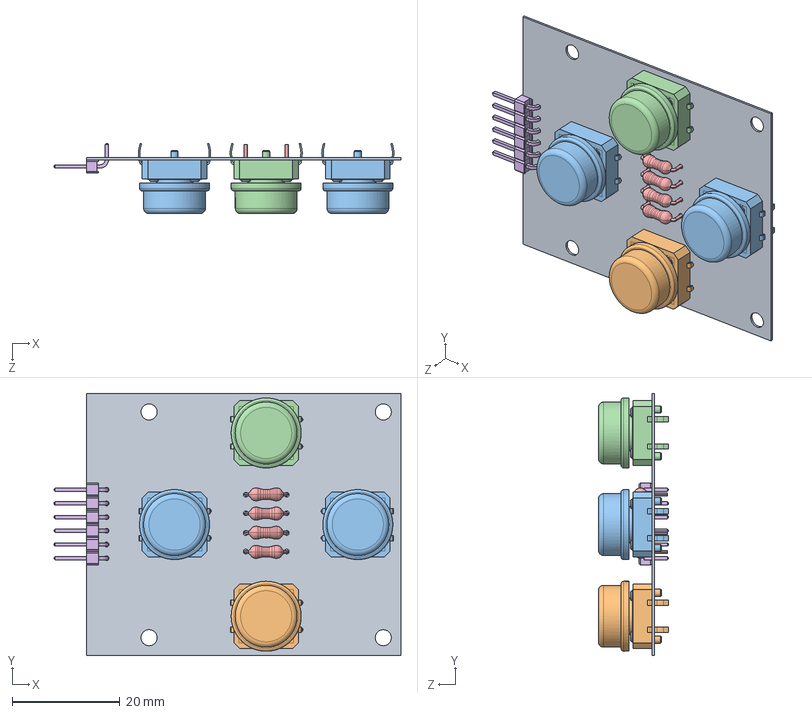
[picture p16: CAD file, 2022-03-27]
mechanical/arrows_keypad/arrowsKeypad.sldasm
64.4 x 48.6 x 13.0 mm
arrowsKeypad
Tactile_12_12_TH_Red_Omron_Switches_2Pos_1
TACTILE_12_12_TH_YELLOW_OMRON_Switches_2Pos_2 x 2
Tactile_12_12_TH_Green_Omron_Switches_2Pos_1
RES_7.62MM_H_TH_Resistors_Single_1 x 4
HEADER_MALE_2.54MM_6_PINS_TH_RIGHT_Terminal_Block_6Pos_2

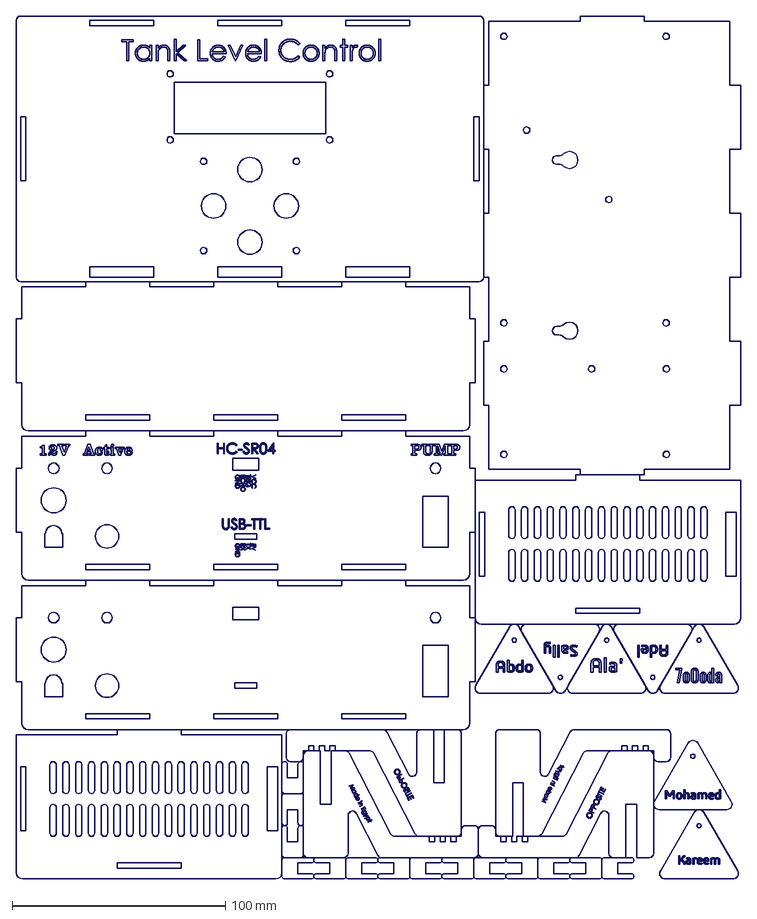
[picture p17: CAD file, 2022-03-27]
mechanical/box/dxf/fullDXF 80_100.DXF
339.5 x 404.5 mm

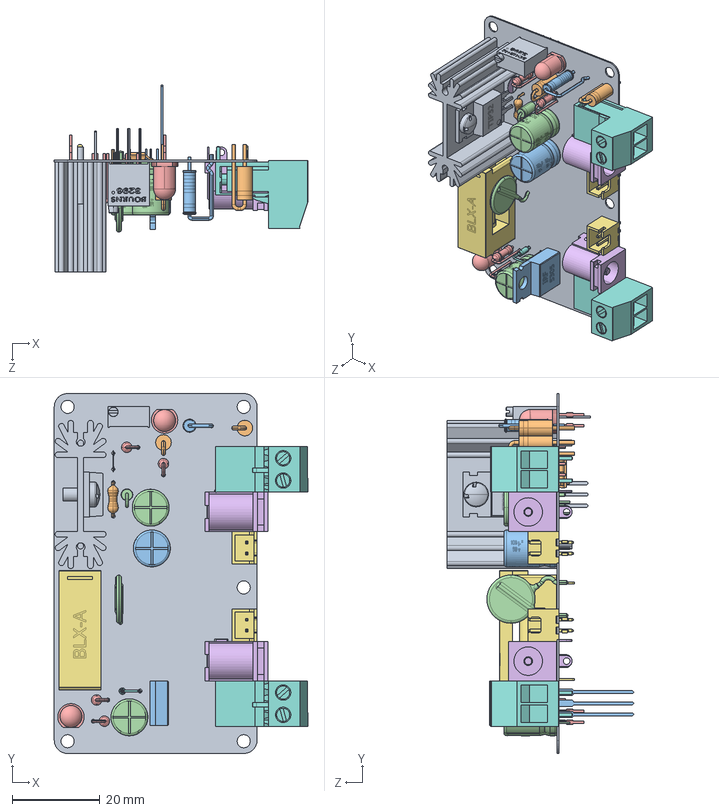
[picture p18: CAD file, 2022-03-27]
mechanical/power_circuit/powerCircuit.sldasm
57.8 x 82.0 x 42.5 mm
powerCircuit
LM317M_SMT_LM317_1
RES_5.08MM_V_TH_Resistors_Single_1
ZENER_2.54MM_V_TH_Zener_1
RES_2.54MM_V_TH_Resistors_Single_1 x 4
CAP_CERAMIC_104_Ceramic_Capacitors_1
FUSE_BLX_5_20_TH_Fuses_1
ZENER_4MM_V_TH_Zener_1
TRIMMER_2.54MM_TH_VariableResistors_1
RES_7.62MM_H_TH_Resistors_Single_1
IRF5305_TH_TO-220_IRF5305_1
VARISTOR_10MM_TH_Varistor_1
LED_5MM_RED_TH_LEDs_Single_1 x 2
DC_POWER_JACK_2.1MM_PJ-002AH_TH_Terminal_Block_2Pos_1 x 2
JST_B2B_TH_Terminal_Block_2Pos_4 x 2
SCREW_TERMINAL_BLOCK__PLUGGABLE5.08MM_TH_GREEN_Terminal_Block_2Pos_2 x 2
TIP32C_TO-220_TH_HEATSINK_TIP32C_1
DIODE_2.54MM_TH_V_Diodes_1 x 2
CAPACITOR_2.54MM_7MMRADIAL_PolarizedCapacitors_1
CAP_5.08MM_RADIAL_PolarizedCapacitors_1 x 2

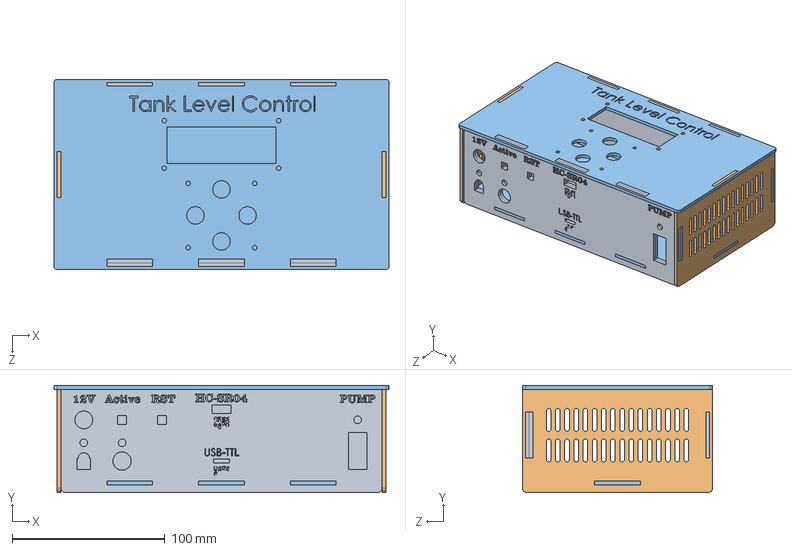
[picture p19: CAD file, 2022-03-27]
mechanical/box/boxAssembly.SLDASM
219.0 x 70.0 x 124.5 mm
boxFront x 3
boxSide x 2
boxTop x 2

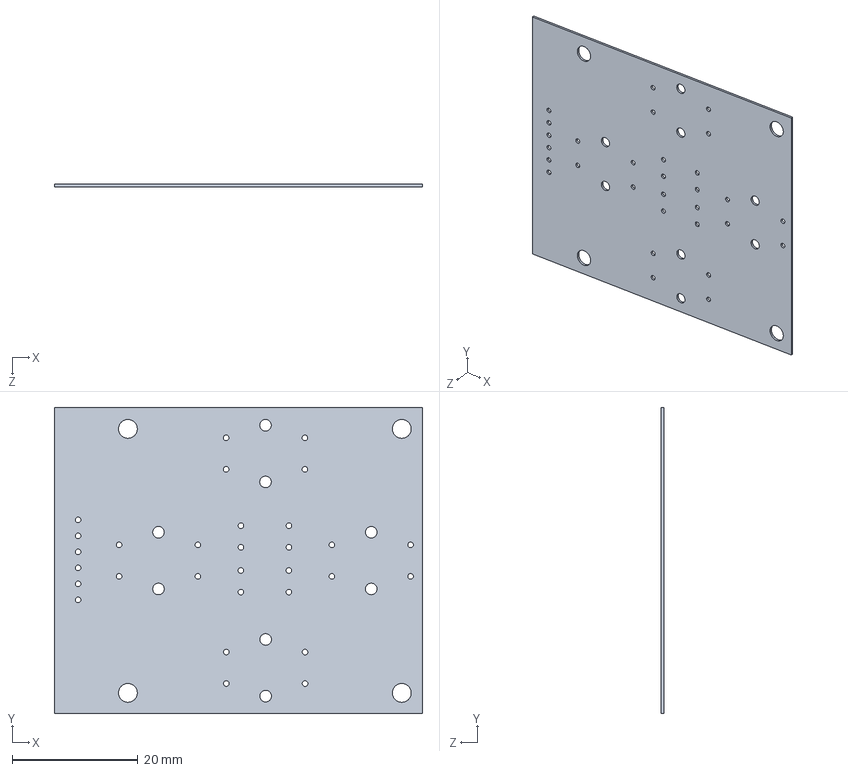
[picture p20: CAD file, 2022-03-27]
mechanical/arrows_keypad/arrowsKeypad/arrowsKeypad.sldprt
58.4 x 48.6 x 0.411 mm

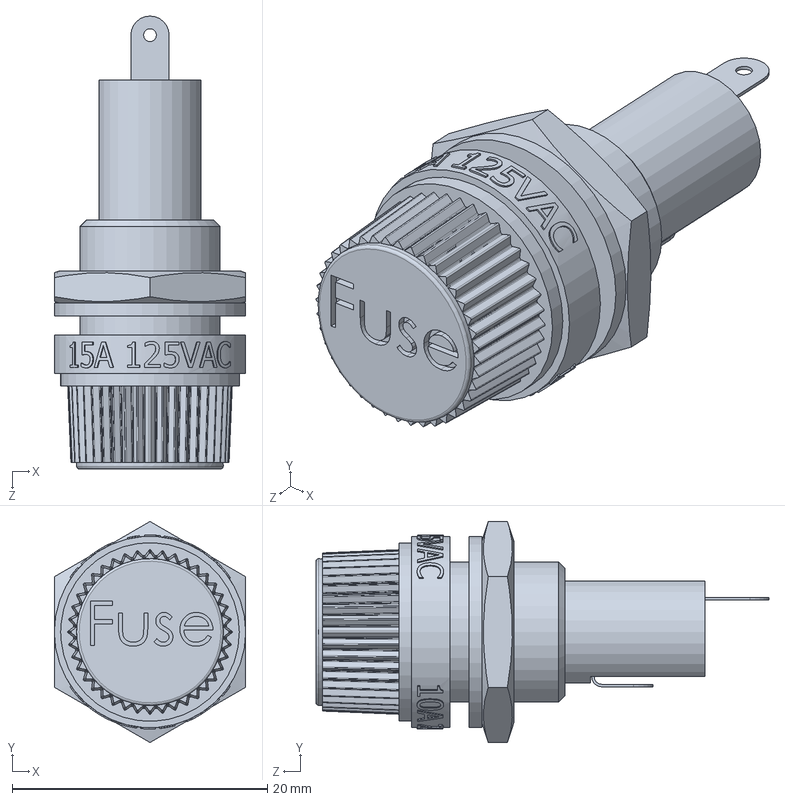
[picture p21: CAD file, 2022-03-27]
mechanical/attachments/Fuse holder.SLDPRT
15.0 x 17.3 x 35.5 mm

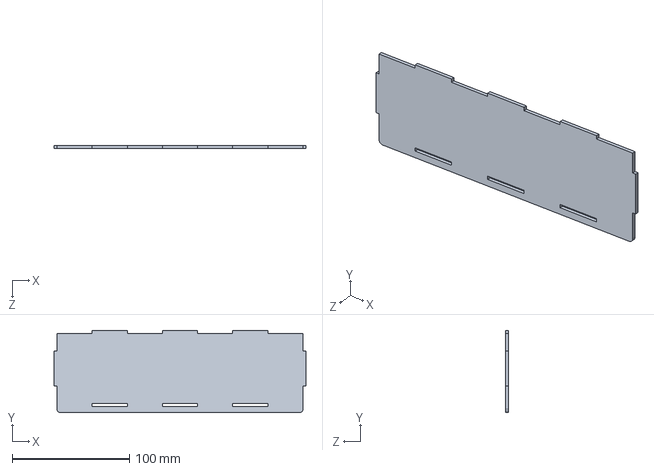
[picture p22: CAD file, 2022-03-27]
mechanical/box/boxFront.SLDPRT
215.0 x 70.0 x 2.50 mm

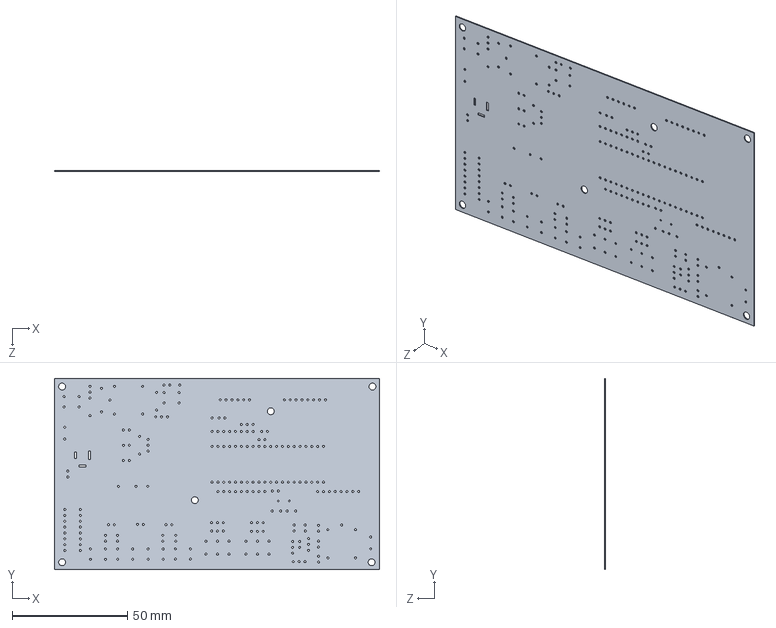
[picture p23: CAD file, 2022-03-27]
mechanical/control_circuit/controlCircuit/controlCircuit.sldprt
140.7 x 82.8 x 0.411 mm

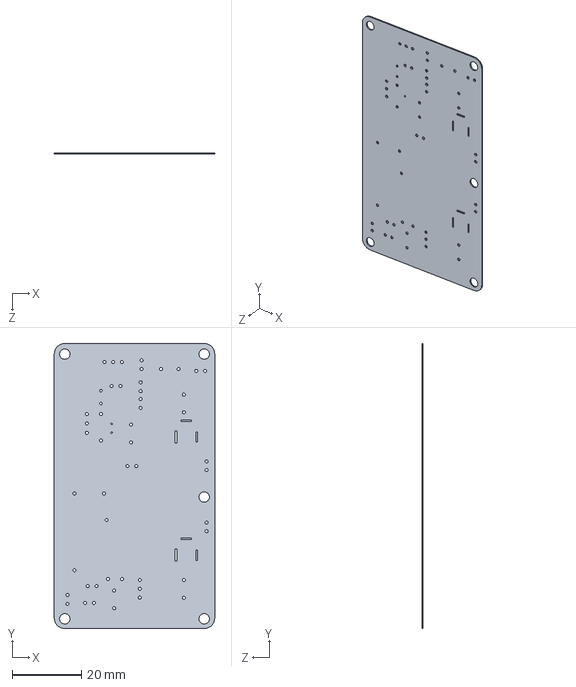
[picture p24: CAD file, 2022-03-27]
mechanical/power_circuit/powerCircuit/powerCircuit.sldprt
46.2 x 82.0 x 0.411 mm

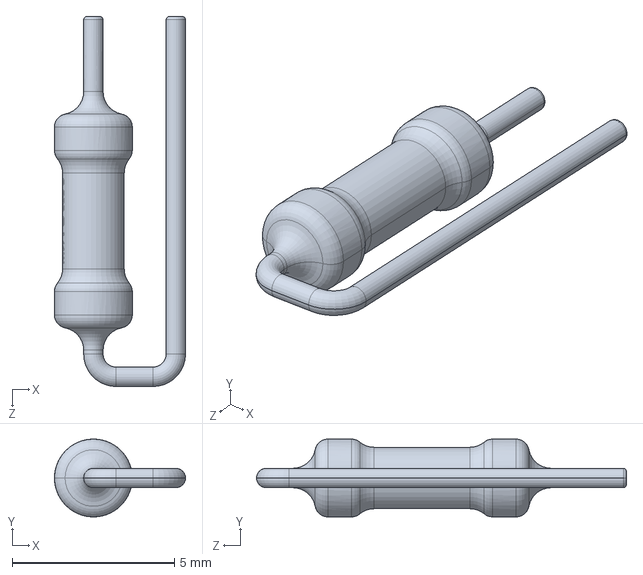
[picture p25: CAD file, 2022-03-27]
mechanical/attachments/RES_2.54MM_V_TH_Resistors_Single_1.sldprt
4.04 x 2.40 x 11.4 mm

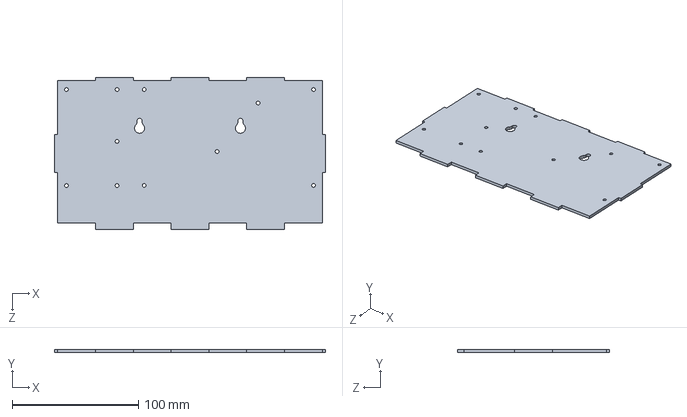
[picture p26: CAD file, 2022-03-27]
mechanical/box/boxTop.SLDPRT
215.0 x 2.50 x 120.5 mm

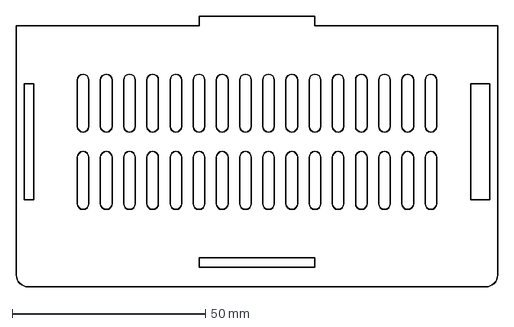
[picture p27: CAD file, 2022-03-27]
mechanical/box/dxf/2-Box Side left.DXF
124.5 x 70.0 mm

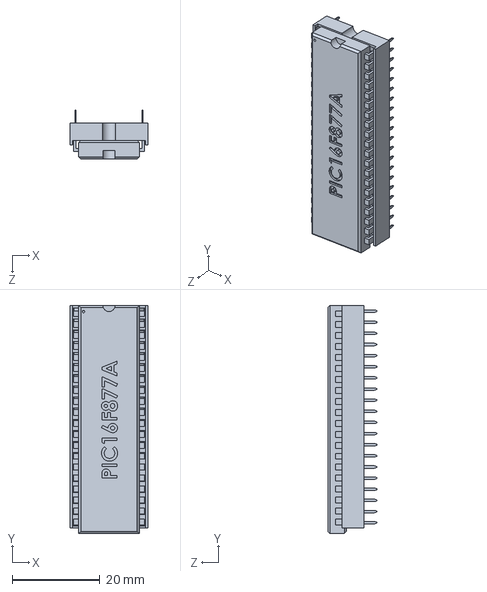
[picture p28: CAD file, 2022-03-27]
mechanical/attachments/PIC16F877A_TH_With_Socket_PIC16F877A_1.sldprt
17.8 x 52.0 x 11.3 mm

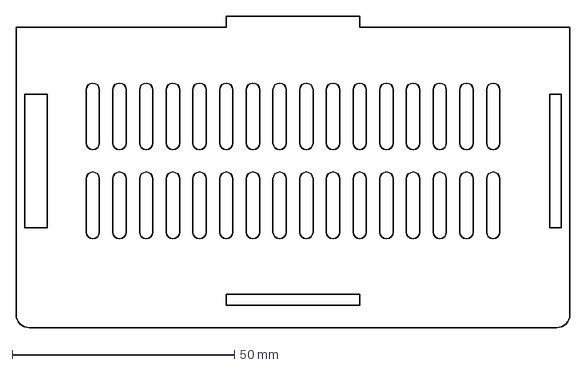
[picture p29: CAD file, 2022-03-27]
mechanical/box/dxf/3-Box Side Right.DXF
124.5 x 70.0 mm

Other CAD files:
mechanical/attachments/LM317M_SMT_LM317_1.sldprt
mechanical/box/boxSide.SLDPRT
mechanical/box/dxf/1-Box Back.DXF
mechanical/attachments/HEADER_MALE_2.54MM_3_PINS_WITH_JUMPER_TH_Terminal_Block_3Pos_1.sldprt
electrical/pcb/arrows_keypad/Arrows Key-EDM/Header_Male_2.54mm_6_Pins_TH_Right_Terminal_Block_6Pos.x_t
electrical/pcb/arrows_keypad/Arrows Key-EDM/Res_7.62mm_H_TH_Resistors_Single.x_t
electrical/pcb/arrows_keypad/Arrows Key-EDM/Tactile_12_12_TH_Green_Omron_Switches_2Pos.x_t
electrical/pcb/arrows_keypad/Arrows Key-EDM/Tactile_12_12_TH_Red_Omron_Switches_2Pos.x_t
electrical/pcb/arrows_keypad/Arrows Key-EDM/Tactile_12_12_TH_Yellow_Omron_Switches_2Pos.x_t
electrical/pcb/arrows_keypad/Arrows Keypad.x_t
electrical/pcb/control_circuit/Control-EDM/Buzzer_7.62mm_pitch_12mm_dia_Speaker.x_t
electrical/pcb/control_circuit/Control-EDM/Cap_Ceramic_104_2.54_Ceramic_Capacitors.x_t
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

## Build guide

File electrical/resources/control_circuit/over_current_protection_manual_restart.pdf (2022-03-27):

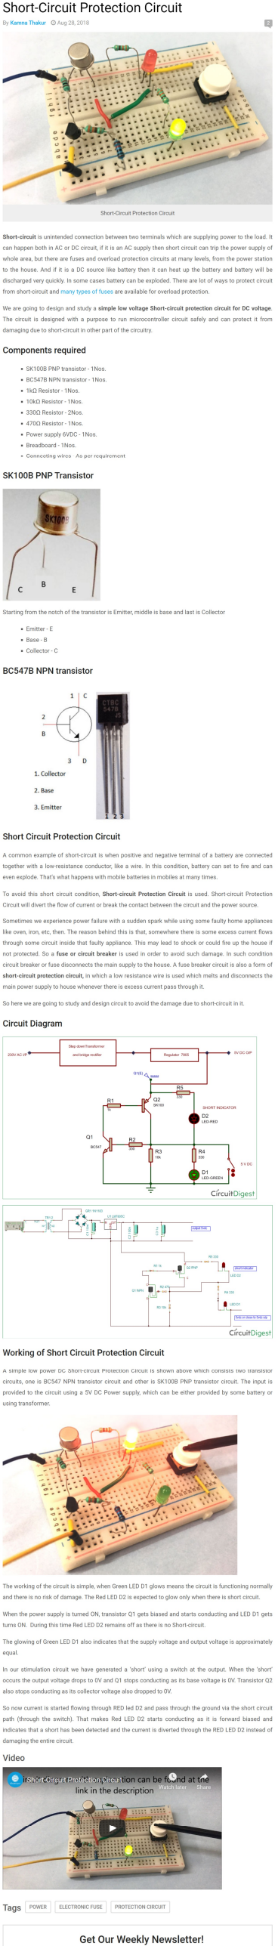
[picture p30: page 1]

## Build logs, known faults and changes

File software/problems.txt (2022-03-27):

When Pump turns on, noise rises up and the text of LCD dims and the MCU reset every few seconds:
	initial Solution: SW solution by storing pump state in the EEPROM. So, after restarting it checks the last state and continue with it.
	Roots Solution : Learn how to avoid electrical noise on PCB.

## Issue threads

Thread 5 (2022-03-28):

Review - how to improve Tank Level Control System?

makaram99, 2022-03-28:
☑️ Do you have any idea how to improve it ?
☑️ Shall we add another section ?
☑️ Is it current content ok ?
☑️ Is readability and navigation good ?

I'm open for ideas. Let's leave a comment !
Or maybe there's no need to do anything more. That's a valid comment too.

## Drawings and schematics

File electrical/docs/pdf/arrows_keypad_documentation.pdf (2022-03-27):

# Arrows Keypad

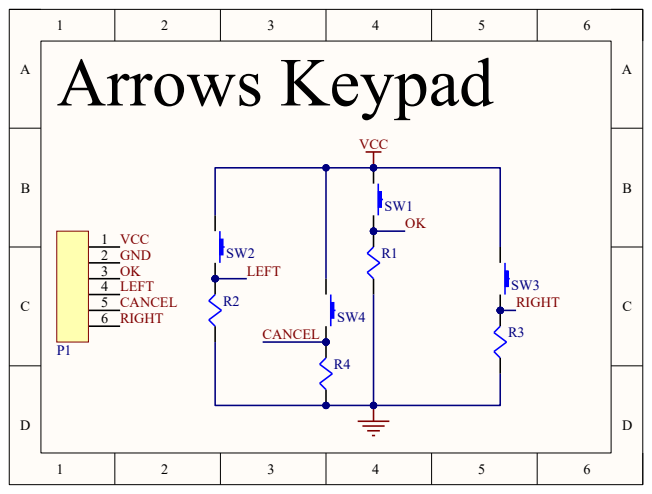
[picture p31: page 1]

# Arrows Keypad

# Board Assembly View

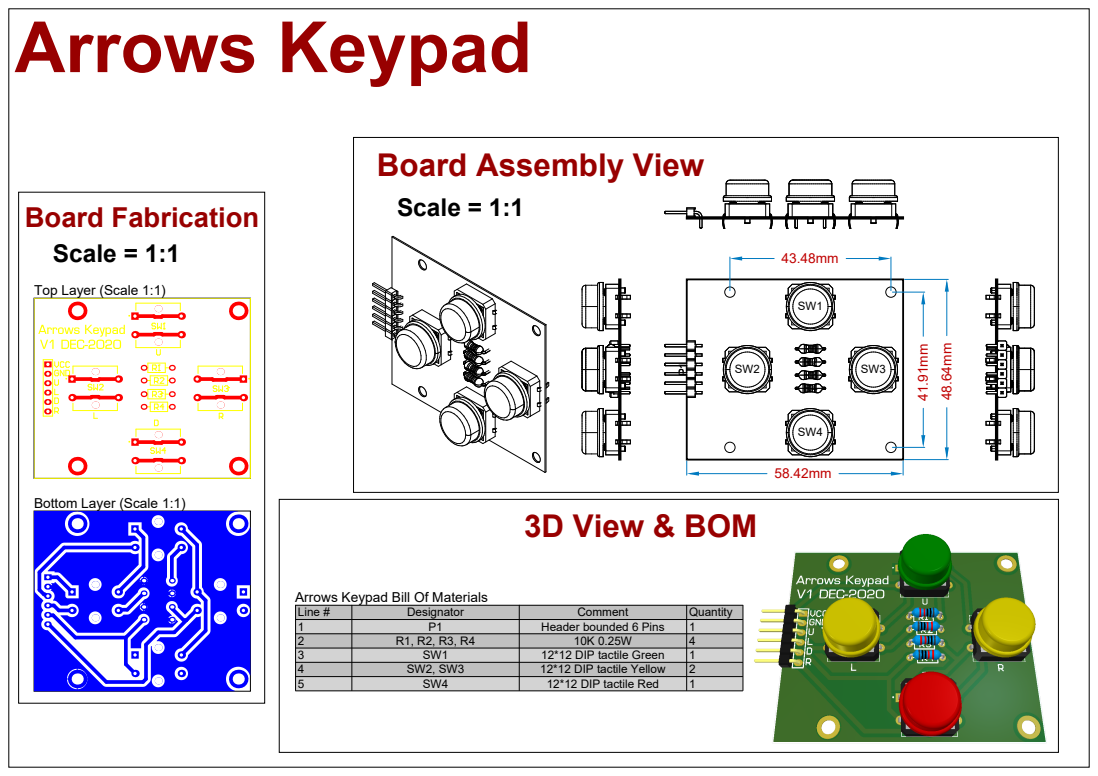
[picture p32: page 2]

Arrows Keypad Bill Of Materials

Line # | Designator | Comment | Quantity
1 | P1 | Header bounded 6 Pins | 1
2 | R1, R2, R3, R4 | 10K 0.25W | 4
3 | SW1 | 12*12 DIP tactile Green | 1
4 | SW2, SW3 | 12*12 DIP tactile Yellow | 2
5 | SW4 | 12*12 DIP tactile Red | 1

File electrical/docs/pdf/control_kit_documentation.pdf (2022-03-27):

U1

Controller | 51%

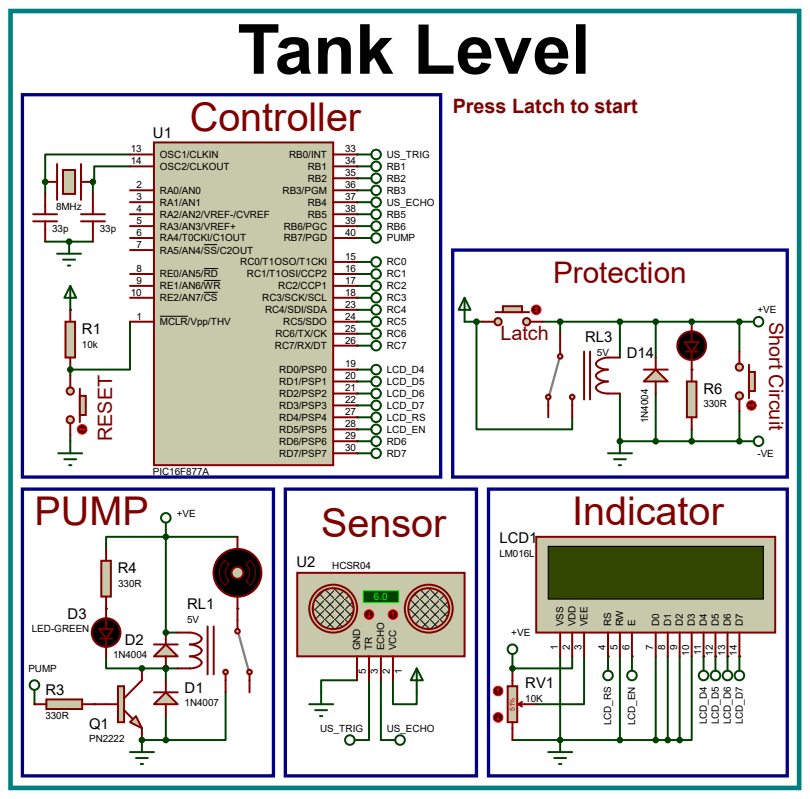
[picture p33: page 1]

Press Latch to start

### R1330R ⁰.25W

# 1- PIC Sh

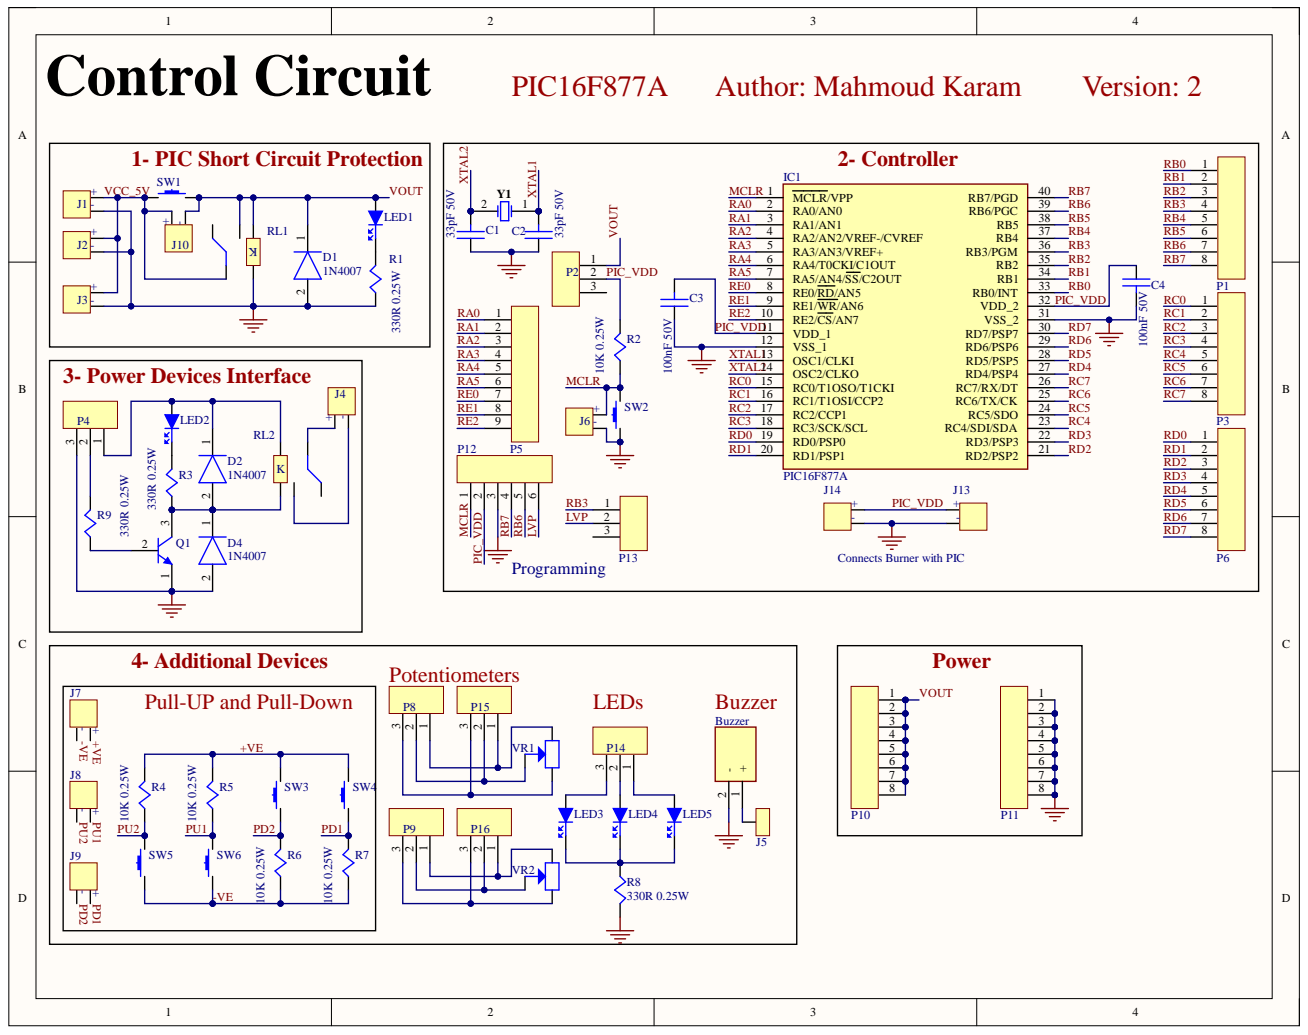
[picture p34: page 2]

Pull-UP and Pull-Down

# Board Assembly View

# Ø3.00mm

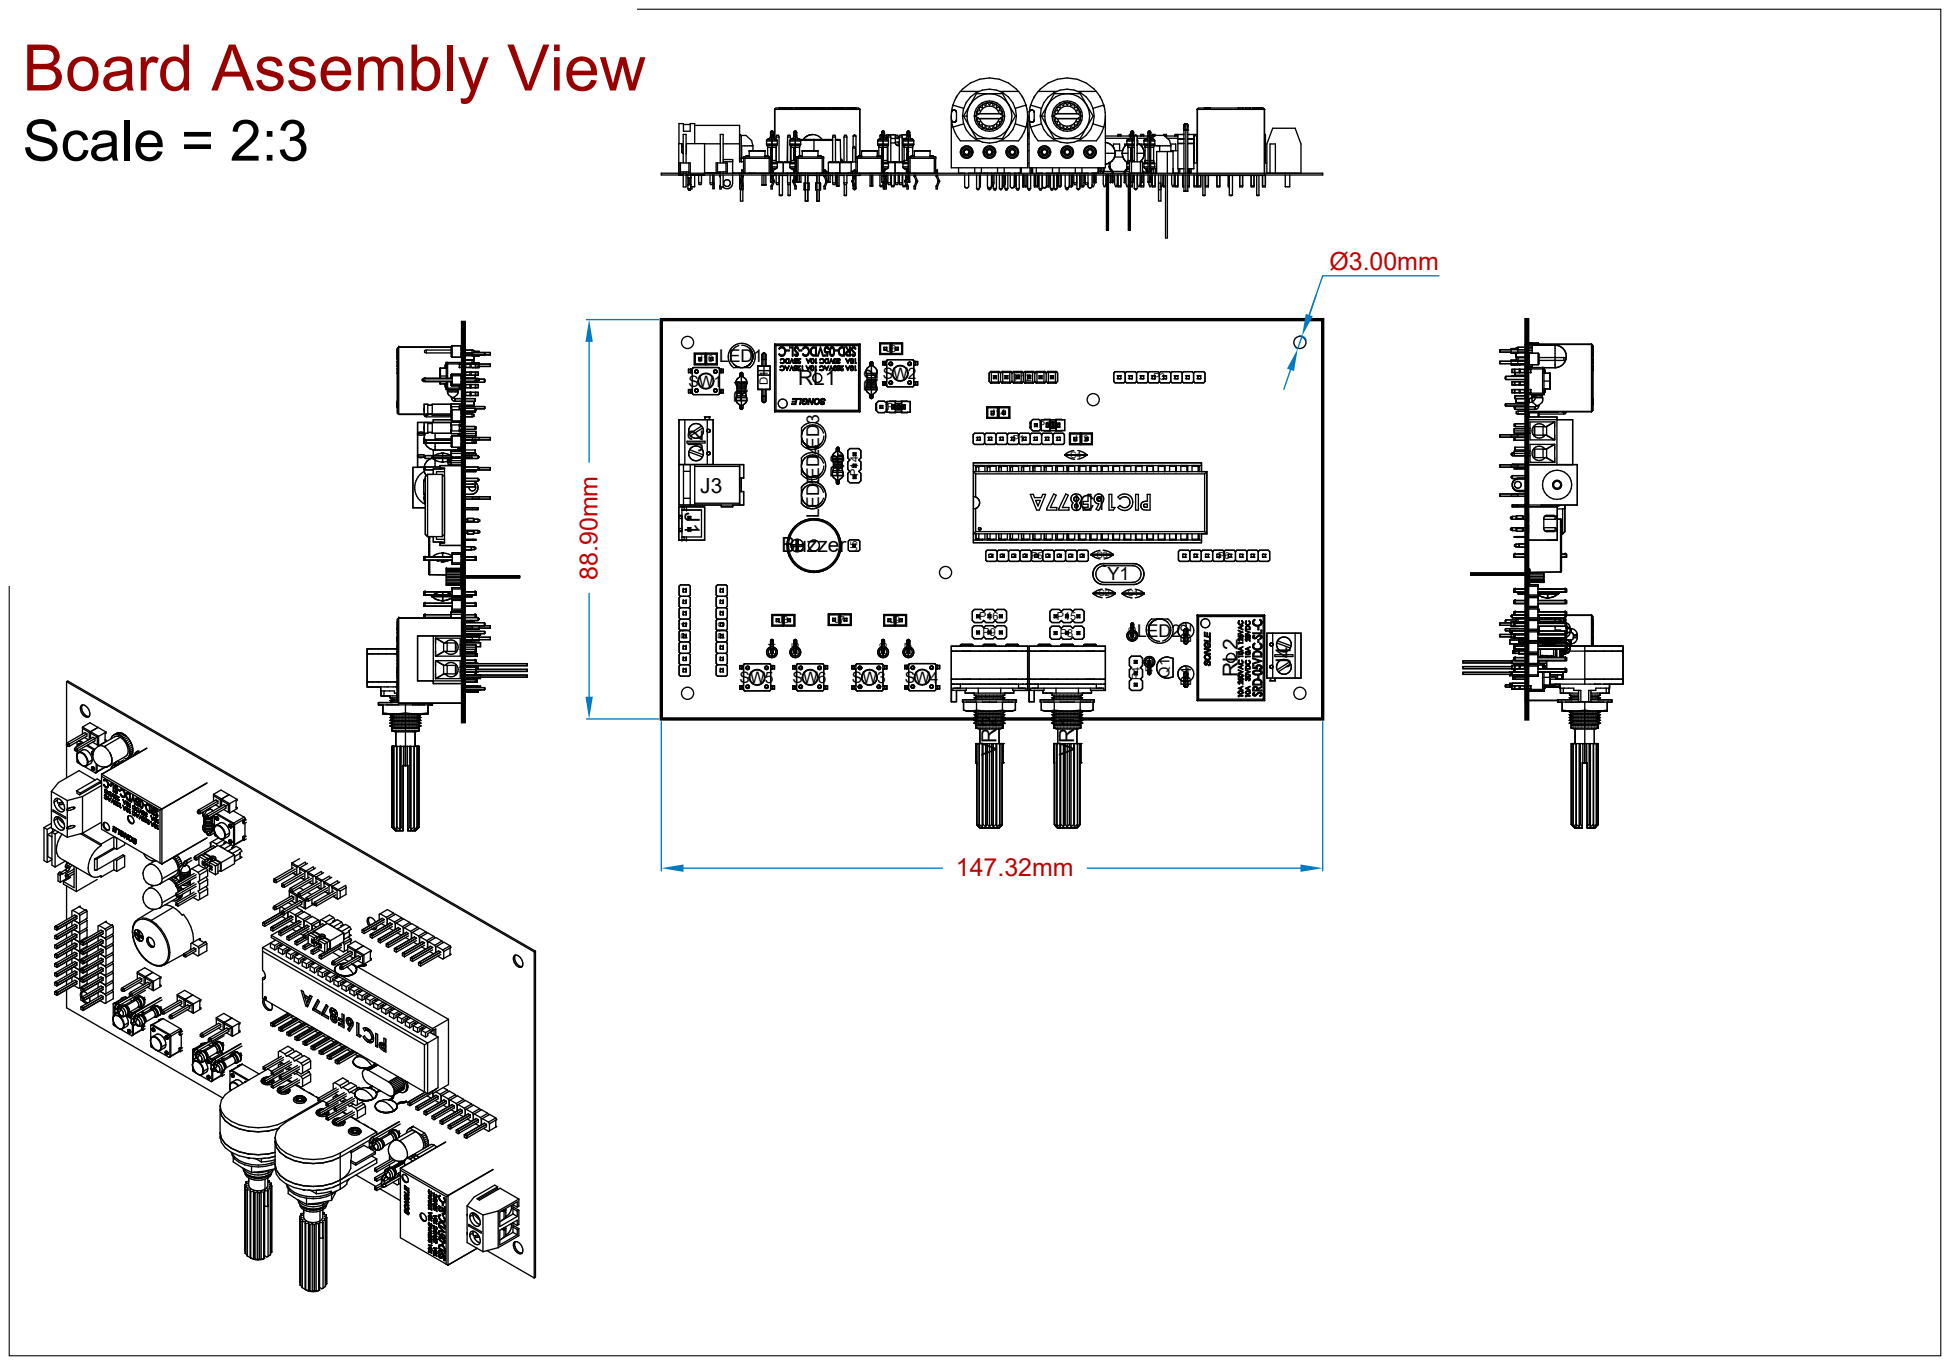
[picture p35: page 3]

Line # | Designator | Comment | Quantity

# Bill Of Materials

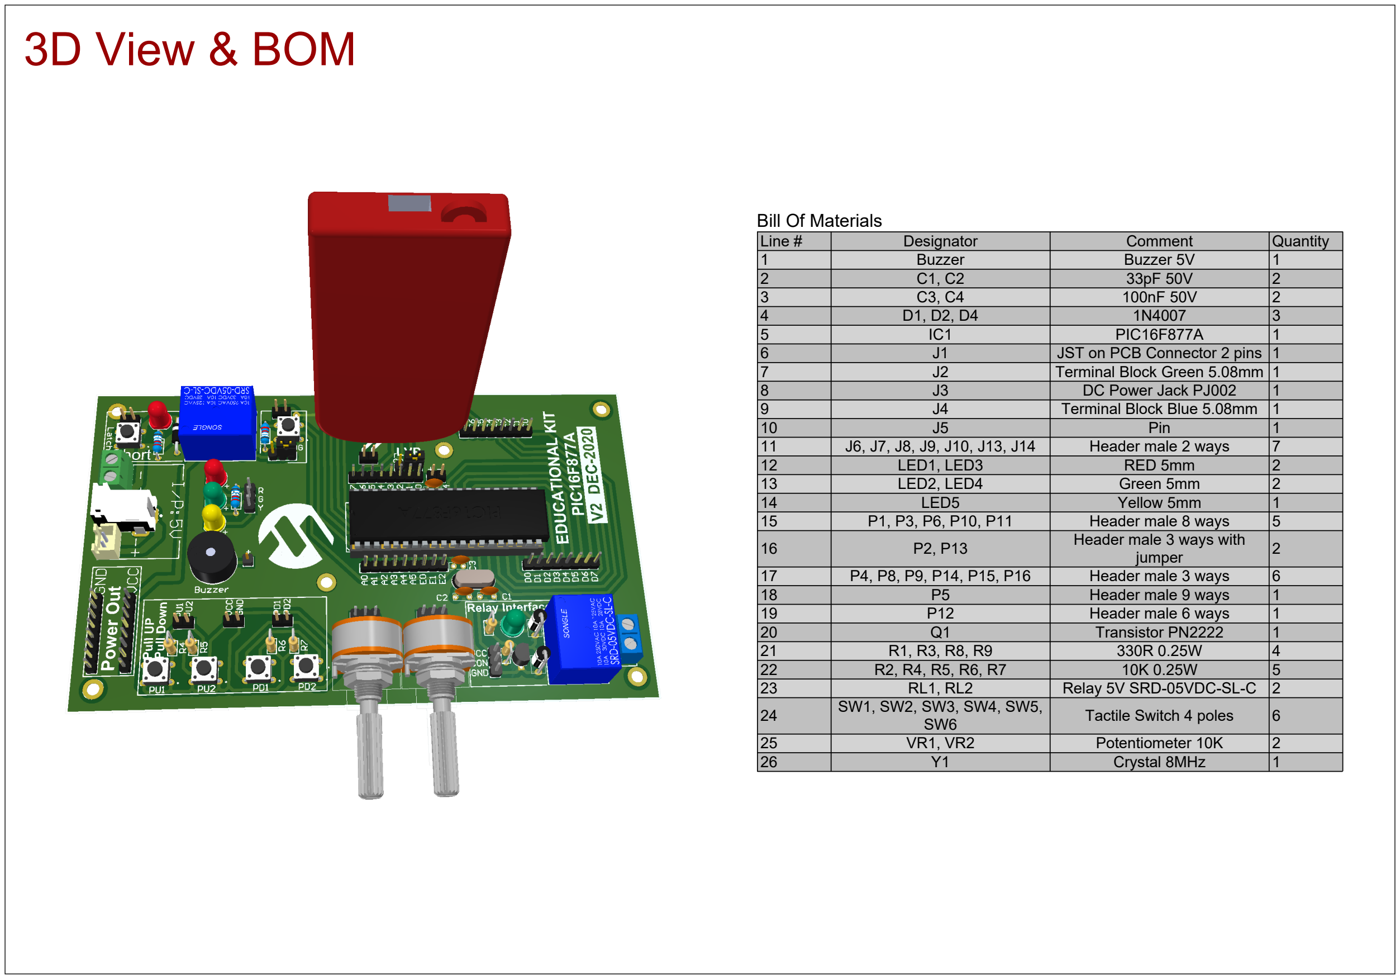
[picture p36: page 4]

1 | Buzzer | Buzzer 5V | 1
2 | C1, C2 | 33pF 50V | 2
3 | C3, C4 | 100nF 50V | 2
4 | D1, D2, D4 | 1N4007 | 3
5 | IC1 | PIC16F877A | 1
6 | J1 | JST on PCB Connector 2 pins | 1
7 | J2 | Terminal Block Green 5.08mm | 1
8 | J3 | DC Power Jack PJ002 | 1
9 | J4 | Terminal Block Blue 5.08mm | 1
10 | J5 | Pin | 1
11 | J6, J7, J8, J9, J10, J13, J14 | Header male 2 ways | 7
12 | LED1, LED3 | RED 5mm | 2
13 | LED2, LED4 | Green 5mm | 2
14 | LED5 | Yellow 5mm | 1
15 | P1, P3, P6, P10, P11 | Header male 8 ways | 5
16 | P2, P13 | Header male 3 ways with jumper | 2
17 | P4, P8, P9, P14, P15, P16 | Header male 3 ways | 6
18 | P5 | Header male 9 ways | 1
19 | P12 | Header male 6 ways | 1
20 | Q1 | Transistor PN2222 | 1
21 | R1, R3, R8, R9 | 330R 0.25W | 4
22 | R2, R4, R5, R6, R7 | 10K 0.25W | 5
23 | RL1, RL2 | Relay 5V SRD-05VDC-SL-C | 2
24 | SW1, SW2, SW3, SW4, SW5, SW6 | Tactile Switch 4 poles | 6
25 | VR1, VR2 | Potentiometer 10K | 2
26 | Y1 | Crystal 8MHz | 1

# 3D View & BOM

# Board Fabrication View

# Scale = 1:1

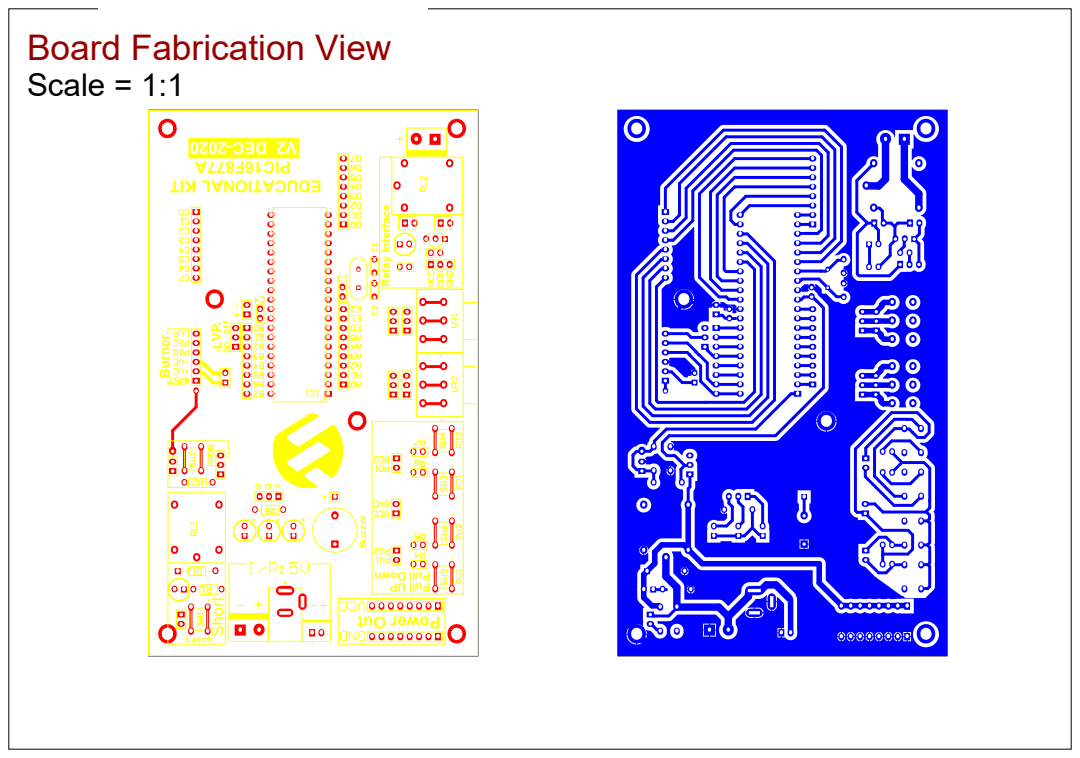
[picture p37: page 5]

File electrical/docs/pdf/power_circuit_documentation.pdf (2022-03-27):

# Author: Mahmoud Karam Version:1

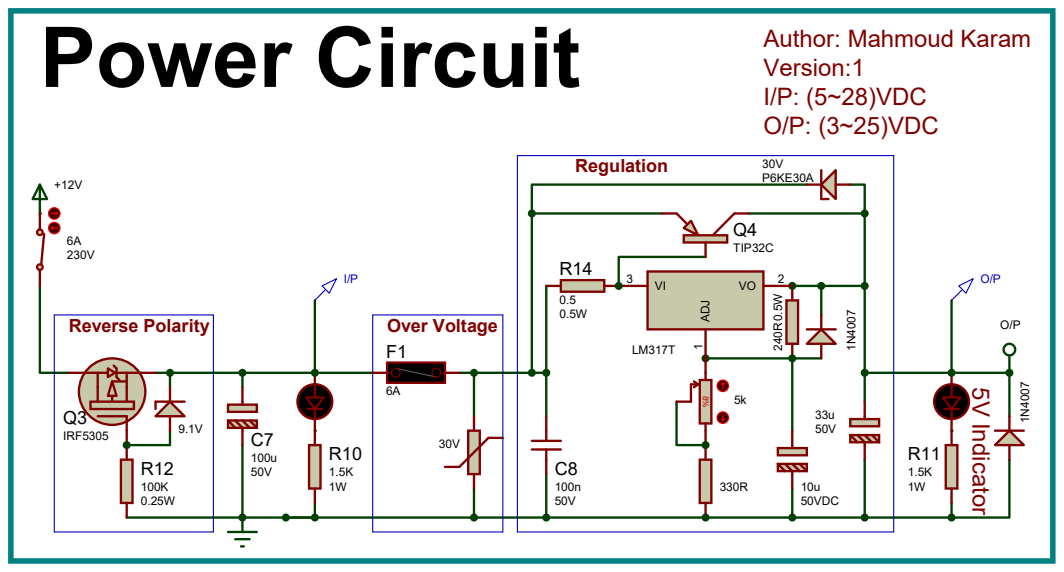
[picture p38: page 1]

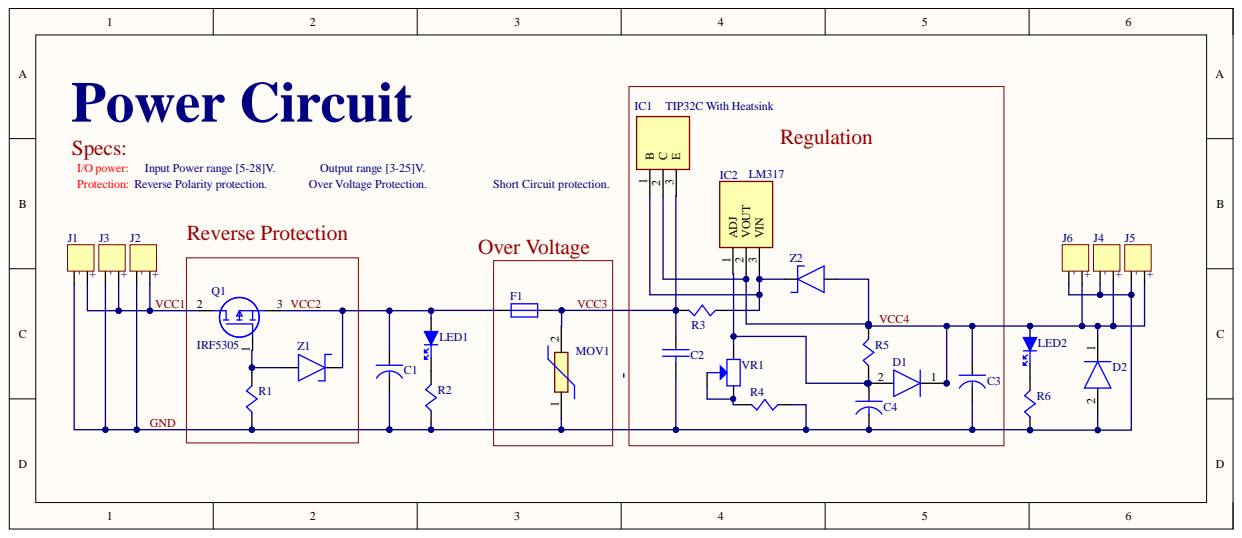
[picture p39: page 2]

# Board Assembly View

# Scale = 1:1

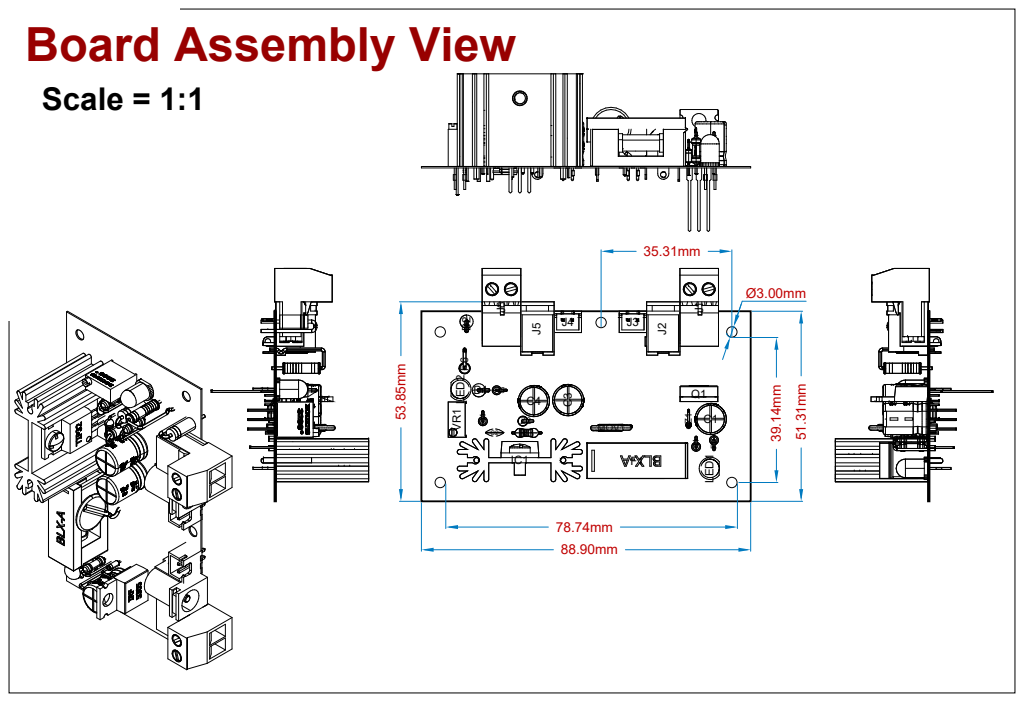
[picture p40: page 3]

# 3D View & BOM

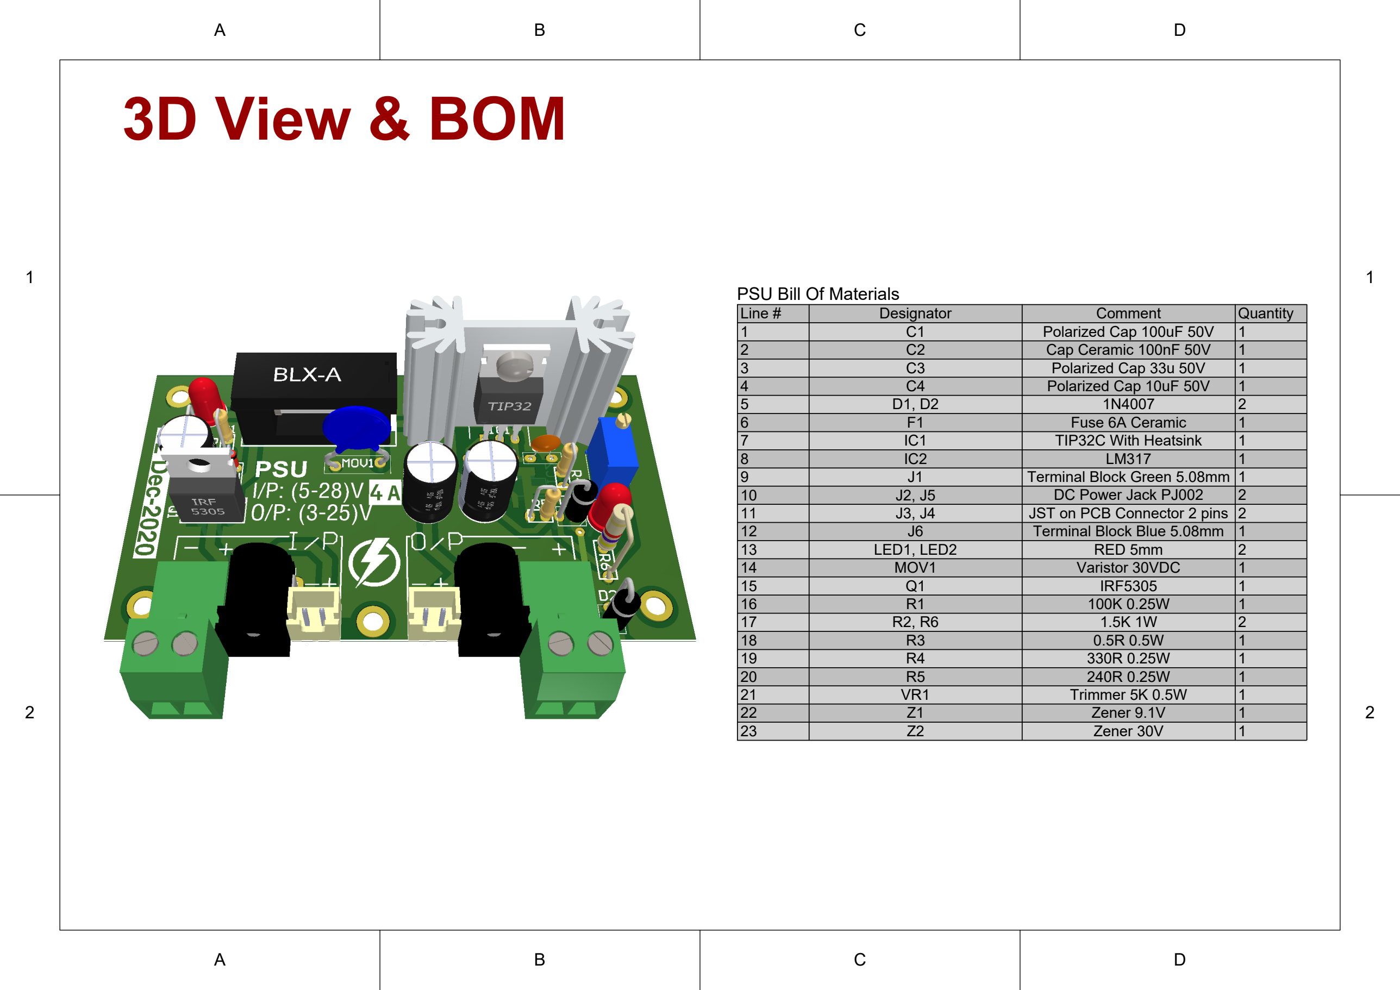
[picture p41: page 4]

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
1 | 1
2 | 2
Line # | Designator | Comment | Quantity
1 | C1 | Polarized Cap 100uF 50V | 1
2 | C2 | Cap Ceramic 100nF 50V | 1
3 | C3 | Polarized Cap 33u 50V | 1
4 | C4 | Polarized Cap 10uF 50V | 1
5 | D1, D2 | 1N4007 | 2
6 | F1 | Fuse 6A Ceramic | 1
7 | IC1 | TIP32C With Heatsink | 1
8 | IC2 | LM317 | 1
9 | J1 | Terminal Block Green 5.08mm | 1
10 | J2, J5 | DC Power Jack PJ002 | 2
11 | J3, J4 | JST on PCB Connector 2 pins | 2
12 | J6 | Terminal Block Blue 5.08mm | 1
13 | LED1, LED2 | RED 5mm | 2
14 | MOV1 | Varistor 30VDC | 1
15 | Q1 | IRF5305 | 1
16 | R1 | 100K 0.25W | 1
17 | R2, R6 | 1.5K 1W | 2
18 | R3 | 0.5R 0.5W | 1
19 | R4 | 330R 0.25W | 1
20 | R5 | 240R 0.25W | 1
21 | VR1 | Trimmer 5K 0.5W | 1
22 | Z1 | Zener 9.1V | 1
23 | Z2 | Zener 30V | 1

PSU Bill Of Materials

# Board Fabrication

# Scale = 1:1

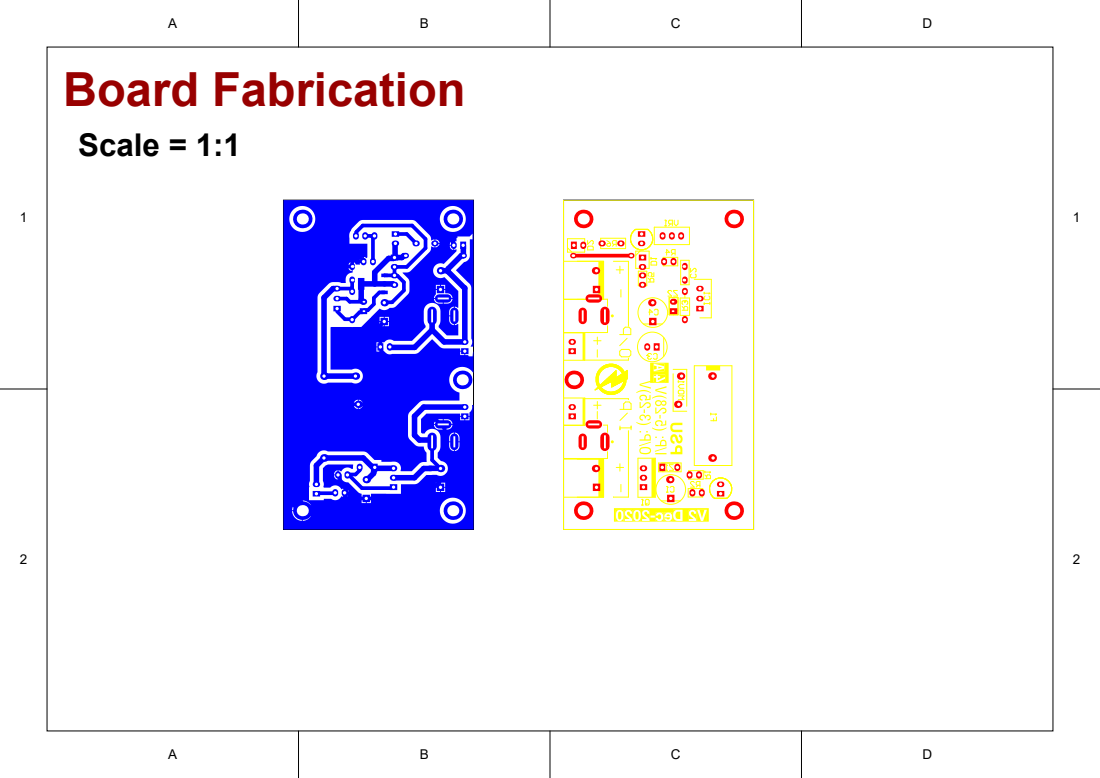
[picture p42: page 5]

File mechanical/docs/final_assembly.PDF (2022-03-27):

SECTION B-B SCALE 1 : 2

Tank Level Control

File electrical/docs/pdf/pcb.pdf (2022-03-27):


0

VR1 0 0

VR1 0


0 VR1 0 0 VR1 0



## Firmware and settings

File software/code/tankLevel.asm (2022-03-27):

_main:

;Tank Level.c,21 :: 		void main() {
;Tank Level.c,23 :: 		unsigned int         time       = 0;         // 4 meters takes time = (11764 *2) uSec = 23526   ==> stored in 16bits ==> 65536
;Tank Level.c,24 :: 		unsigned short int   distance   = 0;         // Maximum depth < 2m(200 cm)   ==> stored in 8bits ==> 256
	CLRF       main_distance_L0+0
	CLRF       main_percentage_L0+0
	CLRF       main_percentage_L0+1
	CLRF       main_i_L0+0
	CLRF       main_state_L0+0
;Tank Level.c,30 :: 		trisb.b6 = 1;                               // Start button as I/P
	BSF        TRISB+0, 6
;Tank Level.c,31 :: 		trisb.b7 = 0;     PUMP            = 0;      // Pump as O/P and initialized with zero
	BCF        TRISB+0, 7
	BCF        PORTB+0, 7
;Tank Level.c,32 :: 		TRISB.b0 = 0;     ULTRASONIC_TRIG = 0;      // Ultrasonic Trigger as O/P and initialized with zero
	BCF        TRISB+0, 0
	BCF        PORTB+0, 0
;Tank Level.c,33 :: 		TRISB.b4 = 1;                               // Ultrasonic Echo as I/P
	BSF        TRISB+0, 4
;Tank Level.c,35 :: 		while (START == 0);                           // Check start button
L_main0:
	BTFSC      PORTB+0, 6
	GOTO       L_main1
	GOTO       L_main0
L_main1:
;Tank Level.c,38 :: 		Lcd_Init();
	CALL       _Lcd_Init+0
;Tank Level.c,39 :: 		Lcd_Cmd(_LCD_CLEAR);
	MOVLW      1
	MOVWF      FARG_Lcd_Cmd_out_char+0
	CALL       _Lcd_Cmd+0
;Tank Level.c,40 :: 		Lcd_Cmd(_LCD_CURSOR_OFF);
	MOVLW      12
	MOVWF      FARG_Lcd_Cmd_out_char+0
	CALL       _Lcd_Cmd+0
;Tank Level.c,42 :: 		T1CON = 0x10;                               //Timer 1 prescalar set to 1:2
	MOVLW      16
	MOVWF      T1CON+0
;Tank Level.c,44 :: 		Lcd_Out(1, 6, "WELCOME");
	MOVLW      1
	MOVWF      FARG_Lcd_Out_row+0
	MOVLW      6
	MOVWF      FARG_Lcd_Out_column+0
	MOVLW      ?lstr1_Tank_32Level+0
	MOVWF      FARG_Lcd_Out_text+0
	CALL       _Lcd_Out+0
;Tank Level.c,45 :: 		Lcd_Out(2, 4, "TANK LEVEL");
	MOVLW      2
	MOVWF      FARG_Lcd_Out_row+0
	MOVLW      4
	MOVWF      FARG_Lcd_Out_column+0
	MOVLW      ?lstr2_Tank_32Level+0
	MOVWF      FARG_Lcd_Out_text+0
	CALL       _Lcd_Out+0
;Tank Level.c,48 :: 		for(i = 0; i <= 3; i++)
	CLRF       main_i_L0+0
L_main2:
	MOVF       main_i_L0+0, 0
	SUBLW      3
	BTFSS      STATUS+0, 0
	GOTO       L_main3
;Tank Level.c,50 :: 		Lcd_Cmd(_LCD_TURN_OFF);
	MOVLW      8
	MOVWF      FARG_Lcd_Cmd_out_char+0
	CALL       _Lcd_Cmd+0
;Tank Level.c,51 :: 		delay_ms(500);
	MOVLW      6
	MOVWF      R11+0
	MOVLW      19
	MOVWF      R12+0
	MOVLW      173
	MOVWF      R13+0
L_main5:
	DECFSZ     R13+0, 1
	GOTO       L_main5
	DECFSZ     R12+0, 1
	GOTO       L_main5
	DECFSZ     R11+0, 1
	GOTO       L_main5
	NOP
	NOP
;Tank Level.c,53 :: 		Lcd_Cmd(_LCD_TURN_ON);
	MOVLW      12
	MOVWF      FARG_Lcd_Cmd_out_char+0
	CALL       _Lcd_Cmd+0
;Tank Level.c,54 :: 		delay_ms(250);
	MOVLW      3
	MOVWF      R11+0
	MOVLW      138
	MOVWF      R12+0
	MOVLW      85
	MOVWF      R13+0
L_main6:
	DECFSZ     R13+0, 1
	GOTO       L_main6
	DECFSZ     R12+0, 1
	GOTO       L_main6
	DECFSZ     R11+0, 1
	GOTO       L_main6
	NOP
	NOP
;Tank Level.c,48 :: 		for(i = 0; i <= 3; i++)
	INCF       main_i_L0+0, 1
;Tank Level.c,55 :: 		}
	GOTO       L_main2
L_main3:
;Tank Level.c,57 :: 		Lcd_Cmd(_LCD_CLEAR);
	MOVLW      1
	MOVWF      FARG_Lcd_Cmd_out_char+0
	CALL       _Lcd_Cmd+0
;Tank Level.c,59 :: 		while(1)                                      // Endless loop
L_main7:
;Tank Level.c,61 :: 		TMR1H = TMR1L = 0;                    // Clearing Timer1 value Registers
	CLRF       TMR1L+0
	MOVF       TMR1L+0, 0
	MOVWF      TMR1H+0
;Tank Level.c,63 :: 		ULTRASONIC_TRIG = 1;
	BSF        PORTB+0, 0
;Tank Level.c,64 :: 		delay_us(10);                         // Tell Ultrasonic to emit ultrasonic waves
	MOVLW      6
	MOVWF      R13+0
L_main9:
	DECFSZ     R13+0, 1
	GOTO       L_main9
	NOP
;Tank Level.c,65 :: 		ULTRASONIC_TRIG = 0;
	BCF        PORTB+0, 0
;Tank Level.c,68 :: 		while(!ULTRASONIC_ECHO);             // Wait for the rising edge from Echo
L_main10:
	BTFSC      PORTB+0, 4
	GOTO       L_main11
	GOTO       L_main10
L_main11:
;Tank Level.c,69 :: 		TMR1ON_bit = 1;                      // Start Timer 1  ==> (T1CON.F0)
	BSF        TMR1ON_bit+0, BitPos(TMR1ON_bit+0)
;Tank Level.c,71 :: 		while(ULTRASONIC_ECHO);              // Wait for the falling edge from Echo
L_main12:
	BTFSS      PORTB+0, 4
	GOTO       L_main13
	GOTO       L_main12
L_main13:
;Tank Level.c,72 :: 		TMR1ON_bit = 0;                      // Stop Timer 1  ==> (T1CON.F0)
	BCF        TMR1ON_bit+0, BitPos(TMR1ON_bit+0)
;Tank Level.c,74 :: 		time = TMR1L | (TMR1H << 8);
	MOVF       TMR1H+0, 0
	MOVWF      R0+1
	CLRF       R0+0
	MOVF       TMR1L+0, 0
	IORWF      R0+0, 1
	MOVLW      0
	IORWF      R0+1, 1
;Tank Level.c,75 :: 		distance    = time / 58.8;
	CALL       _word2double+0
	MOVLW      51
	MOVWF      R4+0
	MOVLW      51
	MOVWF      R4+1
	MOVLW      107
	MOVWF      R4+2
	MOVLW      132
	MOVWF      R4+3
	CALL       _Div_32x32_FP+0
	CALL       _double2byte+0
	MOVF       R0+0, 0
	MOVWF      main_distance_L0+0
;Tank Level.c,76 :: 		distance   += 1;                     // distance calibration
	INCF       R0+0, 0
	MOVWF      R1+0
	MOVF       R1+0, 0
	MOVWF      main_distance_L0+0
;Tank Level.c,78 :: 		if((distance >= MIN_DISTANCE) && (distance <= MAX_DISTANCE))  // Check valid distance
	MOVLW      0
	SUBWF      R1+0, 0
	BTFSS      STATUS+0, 0
	GOTO       L_main16
	MOVF       main_distance_L0+0, 0
	SUBLW      24
	BTFSS      STATUS+0, 0
	GOTO       L_main16
L__main31:
;Tank Level.c,80 :: 		percentage  = 100 - distance * 100 / MAX_DISTANCE;
	MOVF       main_distance_L0+0, 0
	MOVWF      R0+0
	MOVLW      100
	MOVWF      R4+0
	CALL       _Mul_8X8_U+0
	MOVLW      24
	MOVWF      R4+0
	MOVLW      0
	MOVWF      R4+1
	CALL       _Div_16x16_S+0
	MOVF       R0+0, 0
	SUBLW      100
	MOVWF      R2+0
	MOVF       R0+1, 0
	BTFSS      STATUS+0, 0
	ADDLW      1
	CLRF       R2+1
	SUBWF      R2+1, 1
	MOVF       R2+0, 0
	MOVWF      main_percentage_L0+0
	MOVF       R2+1, 0
	MOVWF      main_percentage_L0+1
;Tank Level.c,82 :: 		if   (percentage >= 80)      // Tank is FULL
	MOVLW      0
	SUBWF      R2+1, 0
	BTFSS      STATUS+0, 2
	GOTO       L__main33
	MOVLW      80
	SUBWF      R2+0, 0
L__main33:
	BTFSS      STATUS+0, 0
	GOTO       L_main17
;Tank Level.c,83 :: 		{      PUMP  = 0;         eeprom_write(1,0); state = 0;      }
	BCF        PORTB+0, 7
	MOVLW      1
	MOVWF      FARG_EEPROM_Write_Address+0
	CLRF       FARG_EEPROM_Write_data_+0
	CALL       _EEPROM_Write+0
	CLRF       main_state_L0+0
	GOTO       L_main18
L_main17:
;Tank Level.c,84 :: 		else if        (eeprom_read(1) || percentage <= 16)      // Tank is FULL
	MOVLW      1
	MOVWF      FARG_EEPROM_Read_Address+0
	CALL       _EEPROM_Read+0
	MOVF       R0+0, 0
	BTFSS      STATUS+0, 2
	GOTO       L__main30
	MOVF       main_percentage_L0+1, 0
	SUBLW      0
	BTFSS      STATUS+0, 2
	GOTO       L__main34
	MOVF       main_percentage_L0+0, 0
	SUBLW      16
L__main34:
	BTFSC      STATUS+0, 0
	GOTO       L__main30
	GOTO       L_main21
L__main30:
;Tank Level.c,85 :: 		{      PUMP  = 1;         eeprom_write(1,1); state = 1;      }
	BSF        PORTB+0, 7
	MOVLW      1
	MOVWF      FARG_EEPROM_Write_Address+0
	MOVLW      1
	MOVWF      FARG_EEPROM_Write_data_+0
	CALL       _EEPROM_Write+0
	MOVLW      1
	MOVWF      main_state_L0+0
L_main21:
L_main18:
;Tank Level.c,87 :: 		switch (state)
	GOTO       L_main22
;Tank Level.c,89 :: 		case 1: Lcd_Out(1, 1, "****PUMP  ON****");        break;
L_main24:
	MOVLW      1
	MOVWF      FARG_Lcd_Out_row+0
	MOVLW      1
	MOVWF      FARG_Lcd_Out_column+0
	MOVLW      ?lstr3_Tank_32Level+0
	MOVWF      FARG_Lcd_Out_text+0
	CALL       _Lcd_Out+0
	GOTO       L_main23
;Tank Level.c,90 :: 		case 0: Lcd_Out(1, 1, "****PUMP OFF****");        break;
L_main25:
	MOVLW      1
	MOVWF      FARG_Lcd_Out_row+0
	MOVLW      1
	MOVWF      FARG_Lcd_Out_column+0
	MOVLW      ?lstr4_Tank_32Level+0
	MOVWF      FARG_Lcd_Out_text+0
	CALL       _Lcd_Out+0
	GOTO       L_main23
;Tank Level.c,91 :: 		}
L_main22:
	MOVF       main_state_L0+0, 0
	XORLW      1
	BTFSC      STATUS+0, 2
	GOTO       L_main24
	MOVF       main_state_L0+0, 0
	XORLW      0
	BTFSC      STATUS+0, 2
	GOTO       L_main25
L_main23:
;Tank Level.c,93 :: 		LCD_Plot(percentage);
	MOVF       main_percentage_L0+0, 0
	MOVWF      FARG_LCD_Plot_percentage+0
	MOVF       main_percentage_L0+1, 0
	MOVWF      FARG_LCD_Plot_percentage+1
	CALL       _LCD_Plot+0
;Tank Level.c,94 :: 		}
	GOTO       L_main26
L_main16:
;Tank Level.c,97 :: 		Lcd_Cmd(_LCD_CLEAR);
	MOVLW      1
	MOVWF      FARG_Lcd_Cmd_out_char+0
	CALL       _Lcd_Cmd+0
;Tank Level.c,98 :: 		Lcd_Out(1,1,"**OUT OF RANGE**");
	MOVLW      1
	MOVWF      FARG_Lcd_Out_row+0
	MOVLW      1
	MOVWF      FARG_Lcd_Out_column+0
	MOVLW      ?lstr5_Tank_32Level+0
	MOVWF      FARG_Lcd_Out_text+0
	CALL       _Lcd_Out+0
;Tank Level.c,99 :: 		Lcd_Out(2,1,"================");
	MOVLW      2
	MOVWF      FARG_Lcd_Out_row+0
	MOVLW      1
	MOVWF      FARG_Lcd_Out_column+0
	MOVLW      ?lstr6_Tank_32Level+0
	MOVWF      FARG_Lcd_Out_text+0
	CALL       _Lcd_Out+0
;Tank Level.c,100 :: 		delay_ms(500);
	MOVLW      6
	MOVWF      R11+0
	MOVLW      19
	MOVWF      R12+0
	MOVLW      173
	MOVWF      R13+0
L_main27:
	DECFSZ     R13+0, 1
	GOTO       L_main27
	DECFSZ     R12+0, 1
	GOTO       L_main27
	DECFSZ     R11+0, 1
	GOTO       L_main27
	NOP
	NOP
;Tank Level.c,101 :: 		Lcd_Cmd(_LCD_TURN_OFF);
	MOVLW      8
	MOVWF      FARG_Lcd_Cmd_out_char+0
	CALL       _Lcd_Cmd+0
;Tank Level.c,102 :: 		delay_ms(250);
	MOVLW      3
	MOVWF      R11+0
	MOVLW      138
	MOVWF      R12+0
	MOVLW      85
	MOVWF      R13+0
L_main28:
	DECFSZ     R13+0, 1
	GOTO       L_main28
	DECFSZ     R12+0, 1
	GOTO       L_main28
	DECFSZ     R11+0, 1
	GOTO       L_main28
	NOP
	NOP
;Tank Level.c,103 :: 		Lcd_Cmd(_LCD_TURN_ON);
	MOVLW      12
	MOVWF      FARG_Lcd_Cmd_out_char+0
	CALL       _Lcd_Cmd+0
;Tank Level.c,104 :: 		PUMP = 0;
	BCF        PORTB+0, 7
;Tank Level.c,105 :: 		}
L_main26:
;Tank Level.c,106 :: 		delay_ms(500);
	MOVLW      6
	MOVWF      R11+0
	MOVLW      19
	MOVWF      R12+0
	MOVLW      173
	MOVWF      R13+0
L_main29:
	DECFSZ     R13+0, 1
	GOTO       L_main29
	DECFSZ     R12+0, 1
	GOTO       L_main29
	DECFSZ     R11+0, 1
	GOTO       L_main29
	NOP
	NOP
;Tank Level.c,107 :: 		}                                             // End of while loop
	GOTO       L_main7
;Tank Level.c,108 :: 		}                                               // End of main
L_end_main:
	GOTO       $+0
; end of _main

_LCD_Plot:

;Tank Level.c,110 :: 		void LCD_Plot(unsigned int percentage)
;Tank Level.c,113 :: 		WordToStr(percentage, percentage_txt);
	MOVF       FARG_LCD_Plot_percentage+0, 0
	MOVWF      FARG_WordToStr_input+0
	MOVF       FARG_LCD_Plot_percentage+1, 0
	MOVWF      FARG_WordToStr_input+1
	MOVLW      LCD_Plot_percentage_txt_L0+0
	MOVWF      FARG_WordToStr_output+0
	CALL       _WordToStr+0
;Tank Level.c,114 :: 		Ltrim(percentage_txt);
	MOVLW      LCD_Plot_percentage_txt_L0+0
	MOVWF      FARG_Ltrim_string+0
	CALL       _Ltrim+0
;Tank Level.c,115 :: 		Lcd_Out(2, 1, "=======    ======");
	MOVLW      2
	MOVWF      FARG_Lcd_Out_row+0
	MOVLW      1
	MOVWF      FARG_Lcd_Out_column+0
	MOVLW      ?lstr7_Tank_32Level+0
	MOVWF      FARG_Lcd_Out_text+0
	CALL       _Lcd_Out+0
;Tank Level.c,116 :: 		Lcd_Out(2, 8, percentage_txt);
	MOVLW      2
	MOVWF      FARG_Lcd_Out_row+0
	MOVLW      8
	MOVWF      FARG_Lcd_Out_column+0
	MOVLW      LCD_Plot_percentage_txt_L0+0
	MOVWF      FARG_Lcd_Out_text+0
	CALL       _Lcd_Out+0
;Tank Level.c,117 :: 		Lcd_Out_Cp("%");
	MOVLW      ?lstr8_Tank_32Level+0
	MOVWF      FARG_Lcd_Out_CP_text+0
	CALL       _Lcd_Out_CP+0
;Tank Level.c,118 :: 		}
L_end_LCD_Plot:
	RETURN
; end of _LCD_Plot

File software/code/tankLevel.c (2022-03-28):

/******************************************************************************
 * @file    tankLevel.c
 * @author  Mahmoud Karam (ma.karam272@gmail.com)
 * @brief   Control level of liquid tank either on filling or empting with HC-SR04 ultrasonic and LCD.
 * @version 1.0.0
 * @date    Nov, 17, 2020
 *
 * @copyright Copyright (c) 2021 for Mahmoud Karam
 *            Licensed to the Apache Software Foundation (ASF) under one
 *            or more contributor license agreements.  See the NOTICE file
 *            distributed with this work for additional information
 *            regarding copyright ownership.  The ASF licenses this file
 *            to you under the Apache License, Version 2.0 (the
 *            "License"); you may not use this file except in compliance
 *            with the License.  You may obtain a copy of the License at
 *            http: ;//www.apache.org/licenses/LICENSE-2.0
 *
 *            Unless required by applicable law or agreed to in writing,
 *            software distributed under the License is distributed on an
 *            "AS IS" BASIS, WITHOUT WARRANTIES OR CONDITIONS OF ANY
 *            KIND, either express or implied.  See the License for the
 *            specific language governing permissions and limitations
 *            under the License.
 ******************************************************************************/
#include "headers/LCD_config.h"

#define START PORTB.B6
#define PUMP PORTB.B7
#define ULTRASONIC_TRIG PORTB.B0
#define ULTRASONIC_ECHO PORTB.B4
#define MIN_DISTANCE 0  // Minimum Distance to turn off pump
#define MAX_DISTANCE 24 // Maximum Distance to turn on pump

void LCD_Plot(unsigned int percentage);
void PUMP_OnOff(unsigned short int PUMP_CopyTurnOnOff);

void main(void) {
  /* Variables' definitions              */
  unsigned short int time = 0;           /*!< 4 meters takes time = (11764 *2) uSec = 23526 (< 65536 --> 16 bit) */
  unsigned char distance = 0;      /*!< Maximum depth < 2m = 200 cm (< 256 --> 8 bit) */
  unsigned short int percentage = 0;     /*!< distance percentage (2 bytes to avoid overflow condition in case MAX_DISTANCE is too small and sensor can read 6meters which may make percentage > 255 )    */
  unsigned char i = 0;            
  unsigned char state = 0;         /*!< state of pump (0 = off, 1 = on) */

  /* Define I/P and O/P Pins             */
  trisb.b6 = 1;         /*!< Start button as I/P  */
  trisb.b7 = 0;
  PUMP = 0;             /*!< Pump as O/P and initialized with zero  */
  TRISB.b0 = 0;
  ULTRASONIC_TRIG = 0;  /*!< Ultrasonic Trigger as O/P and initialized with zero  */
  TRISB.b4 = 1;         /*!< Ultrasonic Echo as I/P  */

  /*!< Wait until press Start button */
  while(START == 0)
    ;

  /* Initializing LCD                    */
  Lcd_Init();
  Lcd_Cmd(_LCD_CLEAR);
  Lcd_Cmd(_LCD_CURSOR_OFF);

  T1CON = 0x10; // Timer 1 prescalar set to 1: ;2

  /*!< Initializing LCD                    */
  Lcd_Out(1, 6, "WELCOME");
  Lcd_Out(2, 4, "TANK LEVEL");
  /* Blinking LCD for 3 Sec */
  for(i = 0; i <= 3; i++) {
    Lcd_Cmd(_LCD_TURN_OFF);
    delay_ms(500);

    Lcd_Cmd(_LCD_TURN_ON);
    delay_ms(250);
  }
  Lcd_Cmd(_LCD_CLEAR);

  while(1) {
    TMR1H = TMR1L = 0;    /*!< Reset Timer 1 */

    ULTRASONIC_TRIG = 1;  /*!< Triggering Ultrasonic Sensor */
    delay_us(10);         /*!< 10uSec delay to trigger Ultrasonic Sensor correctly */
    ULTRASONIC_TRIG = 0;  /*!< Stop triggering Ultrasonic Sensor */

    /*!< Wait until Ultrasonic echo is received */
    while(0 == ULTRASONIC_ECHO)
      ;

    TMR1ON_bit = 1;       /*!< Start Timer 1 ==> (T1CON.F0) */

    /*!< Wait until Ultrasonic echo is received */
    while(ULTRASONIC_ECHO)
      ;          

    /*!< Stop Timer 1 and calculate distance */  
    TMR1ON_bit = 0;       
    time = TMR1L | (TMR1H << 8);
    distance = time / 58.8;
    distance += 1;        /*!< Add 1 to avoid distance = 0 */

    /*!< Check if distance is in range */
    if((distance >= MIN_DISTANCE) && (distance <= MAX_DISTANCE)) {
      percentage = 100 - distance * 100 / MAX_DISTANCE;

      /*!< If tank is full, turn off pump */
      if(percentage >= 80) {
        PUMP = 0;
        eeprom_write(1, 0);
        state = 0;
      } else if(eeprom_read(1) || percentage <= 16) { /*!< If tank is empty, turn on pump */
        PUMP = 1;
        eeprom_write(1, 1);
        state = 1;
      }

      switch(state) {
        case 1: ;
          Lcd_Out(1, 1, "****PUMP  ON****");    /*!< Display Pump ON on LCD Row 1, Column 1 */
          break;
        case 0: ;
          Lcd_Out(1, 1, "****PUMP OFF****");    /*!< Display Pump OFF on LCD Row 1, Column 1 */
          break;
      }

      LCD_Plot(percentage);                     /*!< Plot percentage on LCD */
    } else {    /*!< If distance is out of range */
      Lcd_Cmd(_LCD_CLEAR);                      /*!< Clear LCD */
      Lcd_Out(1, 1, "**OUT OF RANGE**");        /*!< Display Out of Range on LCD Row 1, Column 1 */
      Lcd_Out(2, 1, "================");        
      delay_ms(500);
      Lcd_Cmd(_LCD_TURN_OFF);
      delay_ms(250);
      Lcd_Cmd(_LCD_TURN_ON);
      PUMP = 0;
    }

    delay_ms(500);                              /*!< Delay for 500ms before next reading */
  } /* End of while(1) */
}   /* End of main() */

/*!< Plot percentage on LCD */
void LCD_Plot(unsigned int percentage) {
  char percentage_txt[7];
  WordToStr(percentage, percentage_txt);
  Ltrim(percentage_txt);
  Lcd_Out(2, 1, "=======    ======");
  Lcd_Out(2, 8, percentage_txt);
  Lcd_Out_Cp("%");
}

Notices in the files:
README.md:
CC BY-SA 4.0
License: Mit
